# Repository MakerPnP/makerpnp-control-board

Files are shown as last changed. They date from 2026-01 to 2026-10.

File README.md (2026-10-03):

<div align="center">







MakerPnP

</div>

# MakerPnP - Control Board

The system is designed to be a fully-featured, and expandable system for pick-and-place machines. Additionally, it is a
drop-in replacement for CHMT32/48 VA/VB machines and existing cables can be used without rewiring and uses the same
mounting holes.

The system can be used for new PnP machines, or retro fitted to existing ones.

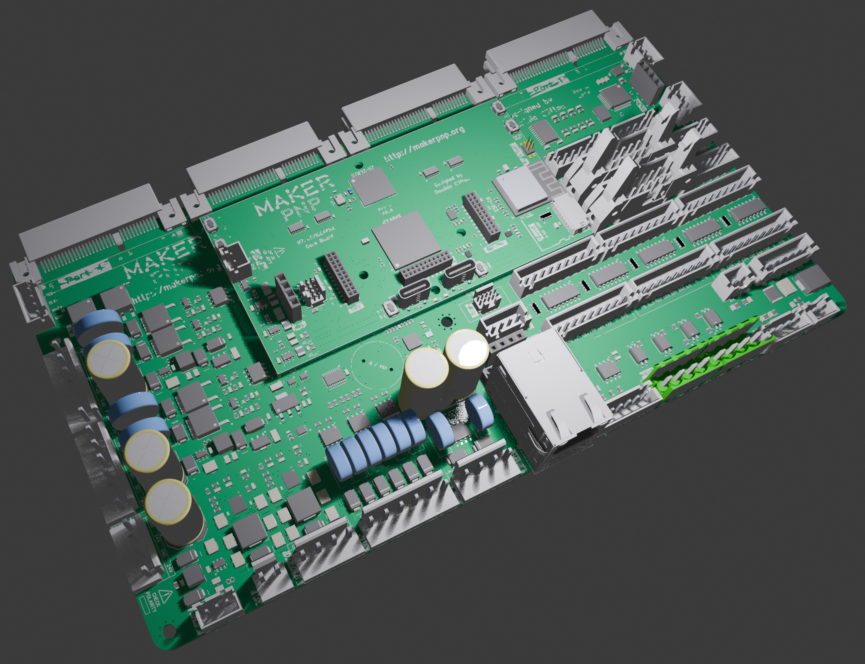
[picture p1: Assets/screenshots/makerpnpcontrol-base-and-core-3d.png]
MakerPnPControl Base and Core PCBs


The system is comprised of two main PCBs, called 'base' and 'core'. A 'core' has the processors and the 'base' has the
connectors for the machine, power-supply circuits, output drivers, protection circuits and other IO circuits and
connectors.  The base board also has expansion slots for things like stepper motor drivers.

The system will use the MakerPnP software and firmware, which is cross-platform and written in Rust. For further details
on the software refer to the following two source repositories:

* Planning software: https://github.com/MakerPnP/makerpnp
* Machine UI software and firmware: https://github.com/MakerPnP/machine

## User Features

* 6 A/B/Z (ABN) differential encoder inputs.
* 8 stepper motor transceiver-driven DIR/STEP signal pairs in 2 banks of 4.
* Emergency stop input on a dedicated hardware interrupt.
* 2x opto-coupled outputs.
* 2x opto-coupled inputs.
* Buzzer
* 8x 5V digital inputs. (end stops, etc)
* 2x 5V 6A regulators, 24V input.
* 5V output connector, e.g. for powering a Raspberry Pi 5.
* 7V output, e.g. for powering head-mounted devices.
* 8x 24V PWM controlled fused and flyback protected outputs.
* 2 pairs of two isolated 48V PWM capable fused and flyback protected outputs. (4x total). e.g. for pumps, heaters, etc.
* Load-cell amplifier.
* 10/100MBit Ethernet (in addition to the Wifi)
* RS422 for remote comms.
* Integrated 7 port USB hub.
* 2x FD-CAN 8Mbps ports.
* 2x I2C muxes and 2 port muxed I2C connector with 4 int signals. (great for identical sensors)
* 4x analog inputs (e.g. for Vacuum, Blow + 2 spare)
* Buttons on the CPU board, with break-out connectors on the main board.
* ETH link/activity LED break-out connector.
* USB connector.

## Expansion port system

The base board features 4x 64-pin expansion slots, each slot has enough signals for driving multiple stepper motors
per board, or for your other expansion ideas.

Each port has the following:
* 2 hardware UARTS.
* 1x SPI + 2x CS pins.
* 1x muxed I2C.
* 2x muxed analog inputs.
* 2x sets of ABN encoder signals. 
* 2x sets of DIAG0/DIAG1 signals.
* 2x 4 channel timers (e.g. for PWM, or 4x pairs of step/direction)
* Clock signals.
* Debug signals.
* Interrupt/Wake signals.
* Card insertion detection system.
* CAN H/L signals.
* USB port.
* 24V and 3.3V inputs.

Additionally, the base board as an RGB led physically located next to each port.

Expansion boards are planed for popular stepper motor drivers.

The slots are at the same physical height as the main board, due to the use of edge-mounted connectors.
Expansion slots can be combined. e.g. it is possible to design a board that plugs into 1,2,3 or 4 ports at the same time.
Note: For high-current expansion boards, it's advised to use power connectors on the expansion board itself.

## Expansion header system

The CPU board features 3 expansion sockets, to allow the connection of expansion cards or debug/development equipment
such as:

* 16 channel logic analyzer (via 16 dedicated FPGA pins).
* additional memory.
* additional sensors.
* other peripherals.

## Developer features

* The cpu/core board expansion headers also allow FPGA flash programming, ESP-C6 programming, H7 programming.
* Debug headers and ports (SWD).
* Boot buttons for H7 and C6.
* Cold-boot select buttons for the FPGA.

## Technical features

* 2 PCB system, a base board and a core board.
* STM32H725IG 550Mhz CPU, 1MB Flash, 564KB RAM (176+25 pin BGA)
* ICE40HX8K FPGA, 7680 logic cells, 128kbit RAM (256 pin BGA)
* ESP32-C6 module, 160Mhz, 4MB Flash, 512KB RAM, Wifi-6, RISC-V, BT 5 LE
* 16MBit shared flash.
* Base board uses 2oz copper 4L PCB.
* Core board used 1oz copper 6L PCB.
* Dedicated 4-bit hardware bus between H7 and FPGA. (OctoSPI1)
* Second 4-bit hardware bus between H7, FPGA, C6 and shared flash.  (OctoSPI2) 

The goal is to make accessing the FPGA and C6 from the H7 seamless by memory mapping them into the H7's address space
using OctoSPI, thus making it possible to send data to/from the FPGA and C6 without a complicated communication protocol.

## Firmware

Firmware is work-in-progress, join the MakerPnP discord server to find out the latest information!

## Status

This status is updated periodically, visit the discord server for the latest information.

### Status overview

| Functionality | Status |
|---|---|
| Base board main VRegs | ✅ - Working |
| Core board main VRegs | ✅ - Working |
| Base board to Core board connectors | 🚧 - Fit is perfect, not all IO lines tested yet |
| H7 Programming Port | ✅ - Working |
| H7 DFU button | ✅ - Working |
| C6 Enable button | ✅ - Working |
| C6 Boot button | ✅ - Working |
| C6 UART Pads | ✅ - Working |
| C6 Activity LED | ✅ - Working, blinky test code flashed via USB port and blinks LEDs |
| STM32H735 | 🚧 - Not all IO lines tested yet |
| ICE40HX8K | 🚧 - Not all IO lines tested yet |
| ESP32-C6 | 🚧 - Not all IO lines tested yet |
| USB hub | ✅ - Detected in Windows, H7 DFU + C6 JTAG working |
| Base board USB sockets | ✅ - Main up-stream socket working, spare hub USB port working | 
| Core board cable bus switches | ✅ - Working, cable works when connected, usb by hub works when cable disconnected |
| Flash | 🚧 - Works with H7 and FPGA, C6 connection untested |
| Ethernet | ✅ - Working well with Embassy-net/SMOL |
| Logic Analyzer Port | ✅ - All 16 IO signals working |
| Digital IO (DIN1-8) | ✅ - Working |
| Buttons | 🚧 - Working, but FPGA cold-boot selection not tested |
| LEDs (2x Activity) | ✅ - Working |
| Buzzer | ✅ - Working |
| Expansion Ports | 🚧 - Port 1 SPI + Wake + CLK + Step1/Dir1 (via mux) working |
| Expansion card detection circuit | ✅ - Working |
| Base board detection circuit | ✅ - Working |
| Timer Muxes | ✅ - Working, signals from FPGA or MCU can be selected |
| Master Reset button | ✅ - Working, powers off Core board regs when pressed |
| TMC5160 Stepper Motor | 🚧 - TMC5160 spins motors, external encoders inputs not tested yet. |
| Base board encoder sockets | ✅ - Working, tested with a 17HS24-2004-ME1K NEMA 17 stepper motor with encoder |
| Emergency stop input | ✅ - Working |
| Base board WS2812 LEDs | ✅ - Working |
| Base board WS2812 external LEDs | ✅ - Working |
| PWM outputs OT1-8 | ✅ - Working via flexible FPGA timer / pwm generation peripheral. | 
| PWM outputs PM1-4 | ✅ - Working via flexible FPGA timer / pwm generation peripheral. |
| HX717 load cell sensor | ✅ - Working. FPGA peripheral working. |
| BCDE/XYZF outputs | ✅ - Working, 8-motor stepper control with sequence based ramp/cruise and pause support |
| Analog In (AIN_VAC/AIN_EXT) | ✅ - Working |
| Analog In Mux (expansion ports 1-4) | ✅ - Working |
| DDIF socket | 🚧 - Not tested, but IC that signals are routed through is working, since encoders work |
| Optical I/O | ✅ - Working. Using 5V supply and 1k0 to GND via buttons for inputs. |
| EXP1 port | 🚧 - Not all IO lines tested yet |
| EXP2 port | 🟦 - Not tested |
| I2C muxes | ✅ - Working.  Both muxes responsive.  One mux tested with 2 pressure sensors that have the same address |
| Pressure sensors | ✅ - Working.  Used XGZP6895D 100KPG and 100KPGN variants (0-100kPa and -100-0kPa respectively) |
| External I2C socket | 🟦 - Not tested |
| External Link/Activity LED socket | 🟦 - Not tested |
| External buttons socket | 🟦 - Not tested |
| Wifi | 🟦 - Not tested |
| SDCard | 🟦 - Not tested |
| CAN 1 | 🟦 - Not tested |
| CAN 2 | 🟦 - Not tested |
| RS422 | 🟦 - Not tested |

### Status log

2026/06/23
 - Much IO is verified and working, code is being written for the FPGA and MCU to validate the hardware.
 - Memory mapped OctoSPI between H7 and FPGA is working well.
 - Stepper motor drivers are working well.

2026/05/30
 - Verification of the hardware is well underway.
 - Errata and Revision history files have been created.

2026/05/06
 - The base, core and stepper1 boards were delivered.

2026/03/13
 - An order for a very small batch of the base board has been placed.
 - the ICE40HX caBGA256 are in short supply, suppliers have 40 week lead times, an order has been placed for a small 
   quantity before suppliers run out.
 - An order for a small batch of the core boards will be placed ASAP.

## Manufacturing files

Refer to PCB Revision History / Errata files before using any files here.

The repo contains files that can be used for manufacturing, however do NOT use any files for manufacturing
PCBs.  Files in the repo are only good for manufacturing when they have been tagged with a git commit that says
'Release To Manufacturing' (RTM).  This is because commits to this repo may make changes to the schematic without
updating the PCB, changes the the PCB without re-exporting gerber or placement files and so on.  Also, there is a lag
between when files are used for manufacturing and when testing and validation is performed.

Example tags that were used for the first round of manufacturing:
```
RTM-MakerPnPBase-RevA-20260313-0241
RTM-MakerPnPCore-RevA-20260313-0242
RTM-MakerPnPCore-RevA-20260405-0022
RTM-MakerPnPStepper1-RevA-20260327-1304
RTM-MakerPnPStepper1-RevA-20260330-0052
```

## Building BOM variants

The MakerPnP `variantbuilder_cli` tool is used to take the exported DipTrace PnP files, along with the parts,
substitutions, and part mapping files, to produce PnP files that use actual parts that can be ordered and placed.

e.g. the schematic might say `CAP_0402`, and `100nF 6.3V 0402`, but additional information is added by substitution rules and
part mappings in order to end up with this:

```
├── C1 (name: 'CAP_0402', value: '100nF 6.3V 0402')
│   └── Substituted (name: 'CAP_0402', value: '100nF 6.3V 0402 X7R 10%'), by (name_pattern: 'CAP_0402', value_pattern: '100nF 6.3V 0402'), comment: 'Use X7R 10% by default'
│       └── Substituted (name: 'CAP_0402', value: '100nF 16V 0402 X7R 10%'), by (name_pattern: 'CAP_0402', value_pattern: '100nF 6.3V 0402 X7R 10%'), de-rate: 'from 6.3V to 16V'
│           └── manufacturer: 'Samsung Electro-Mechanics', mpn: 'CL05B104KO5NNNC' (Auto-selected)
```

Here's how the tools are can be run (from their corresponding directories):
```
$ variantbuilder_cli @MakerPnPControl-core-PnP_variant1.args
$ variantbuilder_cli @MakerPnPControl-PnP_variant1.args
```

Note: the arguments are contained within the `.args` files for easy editing and maintainability.

## Links

Please subscribe to be notified of live-stream events so you can follow the development process.

* Patreon: https://www.patreon.com/MakerPnP
* Source: https://github.com/MakerPnP
* Discord: https://discord.gg/ffwj5rKZuf
* YouTube: https://www.youtube.com/@MakerPnP
* X/Twitter: https://x.com/MakerPicknPlace

## Authors

* Dominic Clifton - Project founder and primary maintainer.

## License

CC-BY-NC - https://creativecommons.org/licenses/by-nc/4.0/

## Contributing

If you'd like to contribute, please raise an issue or a PR on the github issue tracker, work-in-progress PRs are fine
to let us know you're working on something, and/or visit the discord server.  See the Links section above.

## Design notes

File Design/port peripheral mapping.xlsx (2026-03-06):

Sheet: UFBGA176+25 Ports
Port | Timer 1 | EXTIs | Timer 2 | EXTIs | Timer1 to Timer 2 signal | Timer 2 to Timer 1 signal | SPI or DIAG0/1 | EXTIs | UART A | EXTIs | UART B | EXTIs | CH3/4 Extis
1 | TIM1 | 9,11,13,14 | TIM2 | 0,3,10,11 | ITR0 | ITR1 | SPI2 | 3,12,14,15 | USART1 | 9,10 | UART8 | 0,1 | 13,14,10,11
2 | TIM3 | 0,1,5,6 | TIM24 | 11,12,13,14 | ITR2 | ITR12 | SPI4 | 4,5,6,12 | USART3 | 8,9 | USART2 | 5,6 | 5,6,13,14
3 | TIM8 | 6,7,8,9 | TIM5 | 3,10,11,12 | ITR1 | ITR3 | SPI3 | 2,10,11,15 | UART5 | 2,12 | USART10 | 2,3 | 8,9,11,12
4 | TIM4 | 6,7,14,15 | TIM23 | 0,1,2,3 | ITR3 | ITR13 | SPI5 | 6,6,8,9 | UART9 | 0,1 | UART7 | 7,8 | 14,15,2,3
ALL UART B EXTIS are usable when using SPI, a single UART or timers for comms
All Timer 1's have interconnects to Timer 2's (Table 94, Peripheral interconnect matrix details)
All used EXTIs: |  | 0,1,2,3,4,5,6,7,8,9,13,14,15
Port 1 and 3 have higher priority UART EXTIs than Port 2 and 4
Scenarios
1 | Two large TYPE A cards plugged into ports 1/2 and 3/4.
2 | 2x TYPE B cards plugged into port 1 and 3 + 2x TYPE C cards plugged into port 2 and 4
3 | 4x TYPE C cards plugged into ports 1-4
4 | 4x TYPE D cards plugged into ports 1-4
5 | 2x TYPE E cards plugged into ports 2 and 4
 | Other variations/combinations possible with some signals going to the FPGA instead of the MCU.
TYPE A | 1 advanced timer, 1 normal timer, 2x32 bit timers with 4 encoders, 2 SPI + 2 HW NSS, 2 UARTS
TYPE B | advanced timer, 32 bit timer, 2 encoders, 1 spi, 1 HW NSS, 2 uarts
TYPE C | normal timer, 32 bit timer, 2 encoders, 1 spi, 1 HW NSS, 2 uarts
TYPE D | normal timer, 32 bit timer, 2 encoders, 1 spi, 1 HW NSS, 1 uart, 2 exti |  |  |  |  |  | 2xTMC5160 | Encoder signals go to TMC5160
TYPE E | 2 uarts, 2 ABN encoders,bit-bash/MDMA 2 pairs of step/dir on spi pins |  |  |  |  |  | 2xTMC2209 | ABN encoder signals on CH1/2/4 or FPGA encoders, use 2nd UART for 2xEXTI (2xDIAG0), FPGA for index.
Remarks
 | FPGA and MCU share a flash chip. MCU must not drive signals when FPGA boots, SS needs to be correct on boot to tell FPGA how to use the SPI, Flash WP and HOLD need to be correct too.
 | Flash is programmed by the MCU, via OCTOSPI.
 | Flash can be used by the MCU after the FPGA has booted, memory mapped if needed.
 | Backup FPGA images, configuration data and other stuff can be stored on the flash.
 | MCU can communicate with FPGA using SPI pins once FPGA is booted, as long as the FPGA implements an SPI peripheral on the same pins.
 | Need LED on the CDONE signal
 | Need a second SPI CS pin for the FPGA to be able to address either the flash or the FPGA.
 | Each card can have a small I2C flash chip for identification purposes.
 | CDONE used as an input while programming, and as an EXTI afterwards, and can have an LED.

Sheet: UFBFA176+25 Peripherals
Peripheral/IO | Features | Usage | Pins |  |  |  | Pin numbers | Sorted pin numbers
 |  |  | CH1 | CH2 | CH3 | CH4
TIM1 | Advanced,Encoder,16bit,DMA,4CH | Port 1 Encoder A/B/N + NSS2 | PE9 | PE11 | PE13 | PE14 | 9,11,13,14 | 9,11,13,14
TIM2 | Encoder,32bit,DMA,4CH | Step/Dir/Step/Dir | PA0 | PB3(JTDO/TRACESWO) | PB10 | PB11 | 0,3,10,11 | 0,3,10,11
TIM3 | Encoder,16bit,DMA,4CH | Port 2 Encoder A/B/N + NSS2 | PA6 | PB5 | PB0 | PB1 | 6,5,0,1 | 0,1,5,6
TIM4 | Encoder,16bit,DMA,4CH | Port 4 Encoder A/B/N + NSS2 | PB6 | PB7 | PD14 | PD15 | 6,7,14,15 | 6,7,14,15
TIM5 | Encoder,32bit,DMA,4CH | Step/Dir/Step/Dir | PH10 | PH11 | PH12 | PA3 | 10,11,12,3 | 3,10,11,12
TIM6 | DMA,DAC | DAC | PA4 |  |  |  | 4 | 4
TIM7 | DMA,DAC | DAC | #N/A
TIM8 | Advanced,Encoder,16bit,DMA,4CH | Port 3 Encoder A/B/N + NSS2 | PC6 | PC7 | PC8 | PC9 | 6,7,8,9 | 6,7,8,9
TIM12 | NoDMA,2CH | Embassy to use no support for TIM6/7/13/14/16/17 | NONE | NONE | NONE | NONE
TIM13 | NoDMA,1CH |  | NONE | NONE | NONE | NONE
TIM14 | NoDMA,1CH |  | NONE | NONE | NONE | NONE
TIM15 | DMA,2CH | Use to drive MDMA to generate 16 step/dir signals on SPI pins | NONE | NONE | NONE | NONE
TIM16 | DMA,1CH | Port 2 / EXPANSION PORT | PB8 | NONE | NONE | NONE | 8 | 8
TIM17 | DMA,1CH | Port 4 / EXPANSION PORT | PB9 | NONE | NONE | NONE | 9 | 9
TIM23 | Encoder,32bit,DMA,4CH | Step/Dir/Step/Dir | PF0 | PF1 | PF2 | PF3 | 0,1,2,3 | 0,1,2,3
TIM24 | Encoder,32bit,DMA,4CH | Step/Dir/Step/Dir | PF11 | PF12 | PF13 | PF14 | 11,12,13,14 | 11,12,13,14
TIM1_ETR |  | Port 1 / EXPANSION PORT | PG5
TIM8_ETR |  | Port 3 / EXPANSION PORT | PG8
 |  |  | OUT1 | OUT2 | EXTI9
DAC1 |  | EXPANSION PORT | PA4 | #N/A | PH9
 |  |  | SCK | MISO | MOSI | NSS
SPI1 |  | EXPANSION PORT | PA5 | PB4(NJTRST) | PD7 | #N/A
SPI2 |  | Port 1 | PD3 | PB14 | PB15 | PB12 | 3,14,15,12 | 3,12,14,15
SPI3 |  | Port 2 | PC10 | PC11 | PB2 | PA15(JTDI) | 10,11,2,15 | 2,10,11,15
SPI4 |  | Port 3 | PE12 | PE5 | PE6 | PE4 | 12,5,6,4 | 4,5,6,12
SPI5 |  | Port 4 | PH6 | PF8 | PF9 | PF6 | 6,8,9,6 | 6,6,8,9
SPI6 |  |  | #N/A | #N/A | #N/A | #N/A
Need 2x SW NSS for either SPI1 or SPI6
SPI1_NSS_SW_1 |  | EXPANSION PORT | PD10
SPI1_NSS_SW_2 |  | EXPANSION PORT | PF5
SPI2_NSS_2 |  |  | PG3
SPI3_NSS_2 |  |  | PG2
SPI4_NSS_2 |  |  | PG7
SPI5_NSS_2 |  |  | PG15
SPI6_NSS_SW_1 |  | WIFI | #N/A
SPI6_NSS_SW_2 |  | EXPANSION PORT | #N/A
Used GPIO ports for SPI |  |  | A,B,C,D,E,F,H
 |  |  | P1_DQS | P1_NCS | P1_CLK | P1_NCLK | P1_IO0 | P1_IO1 | P1_IO2 | P1_IO3
OCTOSPI1 | permanently memory mapped | FPGA | #N/A | PG6 | PF10 | #N/A | PD11 | PD12 | PC2 | PD13
 |  |  | P2_DQS | P2_NCS | P2_CLK | P1_NCLK | P1_IO4 | P1_IO5 | P1_IO6 | P1_IO7
OCTOSPI2 | conditionally memory mapped | FLASH - NCS to flash and ESP32-C6 FSPIQ and FPGA SPI_SS_B | #N/A | PG12 | PF4 | #N/A | PD4 | PH3 | PC3 | PE10
OCTOSPI2_NCS_2 | conditionally memory mapped | WIFI | PH15
OCTOSPI2_NCS_3 | conditionally memory mapped | EXPANSION_PORT | PE15
OCTOSPI2_NCS_4 | conditionally memory mapped | FPGA | PH1-OSC_OUT
^ NOTE: all OCTOSPI_NCS_x pins are on EXTI15 pin Px15 so use here is flexible
RCC_OSC_IN |  | TCXO, single pin | PH0-OSC_IN
 |  |  | RX | TX
USART1 |  | Stepper 1 | PA10 | PA9 |  |  | 10,9 | 9,10
USART2 |  | Stepper 2 | PD6 | PD5 |  |  | 6,5 | 5,6
USART3 |  | Stepper 3 | PD9 | PD8 |  |  | 9,8 | 8,9
UART4 |  | Head communication (RS422, no flow control) | PD0 | PD1 |  |  | 0,1 | 0,1
UART5 |  | Stepper 4 | PD2 | PC12 |  |  | 2,12 | 2,12
USART6 |  | EXPANSION PORT | PG9 | PG14 |  |  | 9,14 | 9,14
UART7 |  | Stepper 6 | PE7 | PE8 |  |  | 7,8 | 7,8
UART8 |  | Stepper 7 | PE0 | PE1 |  |  | 0,1 | 0,1
UART9 |  | Stepper 5 | PG0 | PG1 |  |  | 0,1 | 0,1
USART10 |  | Stepper 8 | PE2 | PE3 |  |  | 2,3 | 2,3
 |  |  | RX | TX
FDCAN1 |  | Port communications | PH14 | PH13
FDCAN2 |  |  | #N/A | #N/A
FDCAN3 |  | Head/Feeder communications | PG10 | PF7
 |  |  | SDA | SCL
I2C1 |  |  | #N/A | #N/A
I2C2 |  | Muxed between ports | PH5 | PH4
I2C3 |  | EXPANSION PORT | PH8 | PH7
I2C4 |  |  | #N/A | #N/A
EXTI0 |  | UART8_RX | PE0
EXTI1 |  | UART8_TX | PE1
EXTI2 |  | USART10_RX | PE2
EXTI3 |  | USART10_TX | PE3
EXTI4 |  | EXTI4_EMERGENCY_STOP | PG4
EXTI5 |  | USART2_TX | PD5
EXTI6 |  | USART2_RX | PD6
EXTI7 |  | UART7_RX | PE7
EXTI8 |  | UART7_TX | PE8
EXTI9 |  | EXTI9_DAC | PH9
EXTI10
EXTI11
EXTI12
EXTI13 |  | EXTI13_WIFI | PC13
EXTI14 |  | EXTI14_FPGA_INT | PC14-OSC32_IN
EXTI15 |  | EXTI15_FPGA_CDONE | PC15-OSC32_OUT
EXTI0,EXTI1,EXTI2,EXTI3,EXTI4,EXTI5,EXTI6,EXTI7,EXTI8,EXTI9,EXTI13,EXTI14,EXTI15 | 0,1,2,3,4,5,6,7,8,9,13,14,15
 |  | Devices on expansion port can trigger MCU action since the FPGA is an IO expander
DIGITAL_IN_1 |  |  | #N/A
DIGITAL_IN_2 |  |  | #N/A
DIGITAL_IN_3 |  |  | #N/A
DIGITAL_IN_4 |  |  | #N/A
ANALOG_IN_1 |  | Use for Analog MUX output 1 (mux inputs go to ports 1-4) (3v3 only) | PA0_C
ANALOG_IN_2 |  | Use for Analog MUX output 2 (mux inputs go to ports 1-4) (3v3 only) | PA1_C
ANALOG_IN_3 |  | EXPANSION PORT (3v3 only) | PC2_C
ANALOG_IN_4 |  | EXPANSION PORT (3v3 only) | PC3_C
ANALOG_IN_5 |  | Vacuum sense 1 (5V tolerant) | PC0
ANALOG_IN_6 |  | Vacuum sense 2 (5V tolerant) | PH2
PWM_OUT_1 |  | EXPANSION PORT | PB8
PWM_OUT_2 |  | EXPANSION PORT | PB9
PWM_OUT_3 |  |  | #N/A
PWM_OUT_4 |  |  | #N/A
PWM_OUT_5 |  |  | #N/A
PWM_OUT_6 |  |  | #N/A
PWM_OUT_7 |  |  | #N/A
PWM_OUT_8 |  |  | #N/A
EXTI14_FPGA_CDONE |  | For LED too | #N/A
FPGA_CRESET_B |  |  | PF15
 |  |  | DM | DP | ID
USB_OTG_HS |  | Device only, connected to an on-board USB hub | PA11 | PA12 | #N/A
FPGA_DIGITAL_IN_1 |  | Drag pin limit
FPGA_DIGITAL_IN_1 |  | Y endstop
FPGA_DIGITAL_IN_1 |  | X endstop
FPGA_DIGITAL_IN_1 |  | Z cam endstop/center
FPGA_PWM_OUT_1 |  | Drag pin
FPGA_PWM_OUT_2 |  | Head down light
FPGA_PWM_OUT_3 |  | Vacuum switch 1
FPGA_PWM_OUT_4 |  | Vacuum switch 1
FPGA_PWM_OUT_5 |  | Work light
FPGA_PWM_OUT_6 |  | Up light
FPGA_PWM_OUT_7 |  | Vacuum pump
FPGA_PWM_OUT_8 |  | Blow pump
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

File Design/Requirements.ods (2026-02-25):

Requirements |  | Notes | Pin-out TODO | Old Done List
 | Fast MCU | STM32H725, TFBGA100, UFBGA 176+25, LQFP144 ?
 |  | H725 has 4x 32 bit timers (TIM2,TIM5,TIM23,TIM24), H743 only has 2 (TIM2, TIM5)
 | FPGA | iCE40HX8K-CT256, 0.8mm pitch 256-ball caBGA
 | Ethernet port | Connected to MCU
 | Ethernet LED port | 2x LED open-drain outputs + 3V3 + GND |  | Use FPGA to drive signals | Need some LED drivers conneted to the FPGA.
 | USB Hub | 8 ports. Main MCU, FPGA, Head MCU, 4x expansion slots, 1 for PC. FE2.1 chipset. Multi-TT. |  | MCU Done
 | Wifi Module/Flashing port | Header to allow for programming of FPGA and MCU and to support a WIFI module.
 |  | To allow for OTA firmware upgrades on main MCU/FPGA
 |  | Signals: MCU NRST, SPI, UART, FPGA programming + SPI + UART + reset, FPGA+WIFI int and CS.
 | IO swappable between MCU and FPGA | Via 3 pin jumpers per signal.
 |  | e.g. to allow either FPGA to drive stepper signals.
 | CHMT48VB compatible connectors | Only for NEEDED IO, not for ALL IO.
 |  | Must allow existing cables to be plugged in without any rewiring.
 | 4x Expansion connectors | Wire up some FPGA pins to each connector + select MCU peripherals
 |  | USB to each port, connect to primary USB interface on peripheral boards.
 |  | At least 2 sockets need sufficient signals to drive 2x 2.54" stepper motor sockets each, in HARDWARE. | DONE | DONE | DIAG0/1 on unused interface pins, with EXTI
 |  | If sufficient MCU peripherals remain, wire up remaining 2 sockets to support them too.
 |  | Ideally 1x 32 bit timer per socket. Ensure timers have encoder support. | DONE | DONE
 |  | 1x UART per socket. | DONE | DONE
 |  | 1x set of SPI SCK/MOSI/MISO pins per socket. With 2x CS pins. Ideally 1 SPI interface per socket with on hardware NSS signal. | TODO (need 1 extra pin per port) | DONE
 |  | 1x pair of SDA/SCL pins. Each socket shares the same I2C bus, e.g. for enumeration/detection. | DONE, using 4:1 bus switch though | DONE
 | Compatible head-connector | 2x PWM controlled outputs for lights | DONE, using DMA driven PWM | SEE BELOW
 |  | 1x PWM controlled output for drag pin solenoid | DONE, using DMA driven PWM | SEE BELOW
 |  | Input for Z center sensor | DONE | DONE
 |  | Input for Drag pin limit sensor | DONE | DONE
 |  | Input for X endstop | DONE | DONE
 |  | 2x Vacuum sensors (Analog, non-isolated) | DONE | DONE
 | Future head-connector | The idea is for an MCU on the head, with vacuum sensor, vacuum switches, lighting, etc.
 |  | [RS422|CAN|USB],5V, 24V, GND - head cable is LONG in this machine, ~2m | DONE, UART OR CAN from MCU, same pins on MCU | UART+CAN from MCU
 |  | 2+2 differential line driver inputs/outputs
 | Chassis digital inputs | Input for Y endstop | DONE | DONE
 | 2x 24V high current PWM controlled outputs | Vacuum pump and Blow pump | DONE, using dedicated PWM timers | DONE
 | 6x 24V medium current PWM controlled outputs | Drag pin solenoid, 3x lights, 2x vacuum switches. | DONE, using DMA driven PWM | DONE
 | 4x PWM fan headers | With RPM feedback | NOT ENOUGH FPGA pins, no space for connectors. | FPGA for PWM and RPM feedback
 |  | Ensure there are 4 PWM circuits connected to the FPGA.
 | 2x Differential Encoder inputs | CHMT48VB only has encoders on X + Y motors. | DONE, via FPGA | Use TIM23 + TIM24 (CH1/CH2 on each)
 |  | Use hardware timers for encoder sampling by hardware. |  | DONE
 | Emergency Stop Input | Should be connected to an EXTI pin and/or TIM_BK input | DONE, EXTI0 | DONE
 | Stepper motor outputs | X Step/Dir | DONE, Via PORT_1 Timer 1 CH1/2
 |  | Y Step/Dir | DONE, Via PORT_1 Timer 1 CH3/4
 |  | L Nozzle Step/Dir | DONE, Via PORT_3 Timer 1 CH1/2
 |  | R Nozzle Step/Dir | DONE, Via PORT_3 Timer 1 CH3/4
 |  | L Feeder Step/Dir | DONE, Via PORT_2 Timer 1 CH1/2
 |  | R Feeder Step/Dir | DONE, Via PORT_2 Timer 1 CH3/4
 |  | Spare Step/Dir 1 | DONE, Via PORT_3 Timer 1 CH1/2
 |  | Spare Step/Dir 2 | DONE, Via PORT_3 Timer 1 CH3/4
 | Buzzer | No need for PWM for it, but can if needed. | DONE
 | 5V 3A output, for Raspberry Pi 5
 |  | Comms for Raspberry Pi to use ethernet
 | 2x connectors for X/Y end-stops | To allow for optical limit switches to be used
 |  | Also to allow for better routing of the Y end-stop wire.
 |  | Rerouting requires purchase of male to female 2 pin XH cable and repinning it and wiring the socket from the cable to the existing harness.
 |  | 3v3, IN, GND
 | 4x Digital inputs 5V tolerant. | Non-isolated in CHMT design. | DONE,PC0,PC3,PH2,PH3 all FT_ha | DONE
 | Analog inputs AI1-4 may need to be 5V tolerant | Non-isolated in CHMT design. | PA0_C,PA1_C,PC2_C,PC3_C are all TT_a, 3v3 ONLY | DONE
 | 2x Digital expansion/pass-though connector. | The idea is that a simple pass-though PCB can be made to route signals between the MCU and FPGA and OR to an expansion connector.
 |  | i.e. MCU -> FPGA or Expansion, FPGA -> MCU or expansion.
 |  | Route all remaining FPGA pins to some high-density connector
 |  | Route remaining FPGA pins to some high-density connector
 |  | Ideally connectors arranged so that the board cannot be inserted incorrectly, even when the same plugs/sockets are used.
 |  | 5V, 3V3, GND, no 24V.
 | Logic expansion header (2.54mm) | Route some pins from the expansion/passthough connector to a logic expansion header
 |  | 24V, 5V, 3V3,GND
Would be nice
 | DCMI camera interface
 | I2C switch | For I2C vacuum sensors that have the same address | DONE, use a 4:1 bus switch on I2C3
 |  | Or enough I2C headers on STM32 I2C peripherals
 | 4x I2C headers | 3v3,GND,SDA,SCL
 | 2x 2.54" stepper motor sockets | But maybe just make a peripheral board, with 2 on each for now
 | 2x Opto Isolated outputs |  | DONE, noted on FPGA pins list
 | 2x Opto Isolated inputs |  | DONE, noted on FPGA pins list
 | 2-4x additional 24V high current PWM controlled outputs
 | 2-4x additional 24V medium current PWM controlled outputs
 |  | The idea is to use 16 GPIO pins (pin1-8 plus pin 9-16 from two ports, or pins 1-16 from a single port) so that PWM can be controlled for each pin via a DMA stream using the GPIO-ODR[H/L] registers.
 |  | Ideally divide 2 16 bit timers over those pins, so that some pins can be GPIO+DMA driven and others can be hardware driven.
Machine external facing ports
 | Front panel USB socket | For USB sticks, OTG.
 | Side/Rear Ethernet port
 | Side/Rear USB port
Make a small PCB to mount to the case
 | RJ45+USB in
 | RJ45+USB out
 | 2x LED input signals + 3v3 + GND
 | 2x LEDs on RJ45 connector
TODO
 | Think about additional FPGA connectors.
 | Think of uses for the 3 unused timers TIM13/14/16, each with capture compare. | Probably use 2 timers for 2 additional high current PWM outputs

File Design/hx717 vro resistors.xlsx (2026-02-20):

VRO | R1 | R2
4.44 | 30000 | 10000
4.7952 | 33200 | 10000
3.8739 | 24900 | 10000

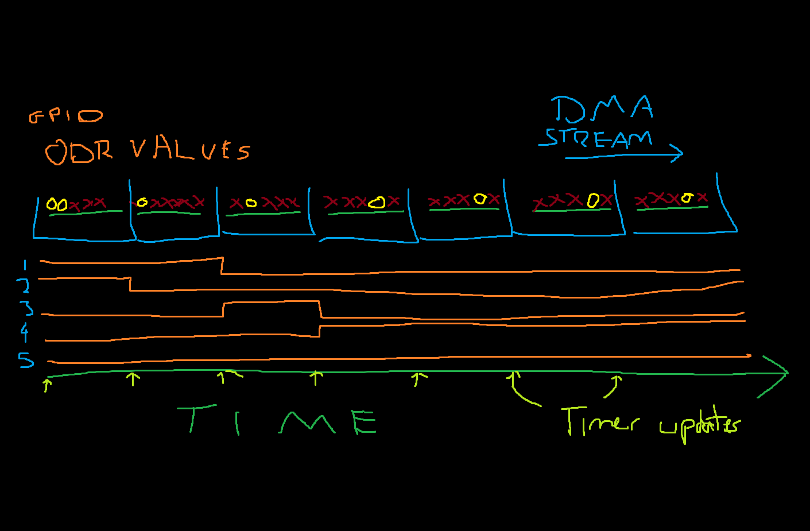
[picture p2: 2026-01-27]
Design/gpio dma for pwm signals.png

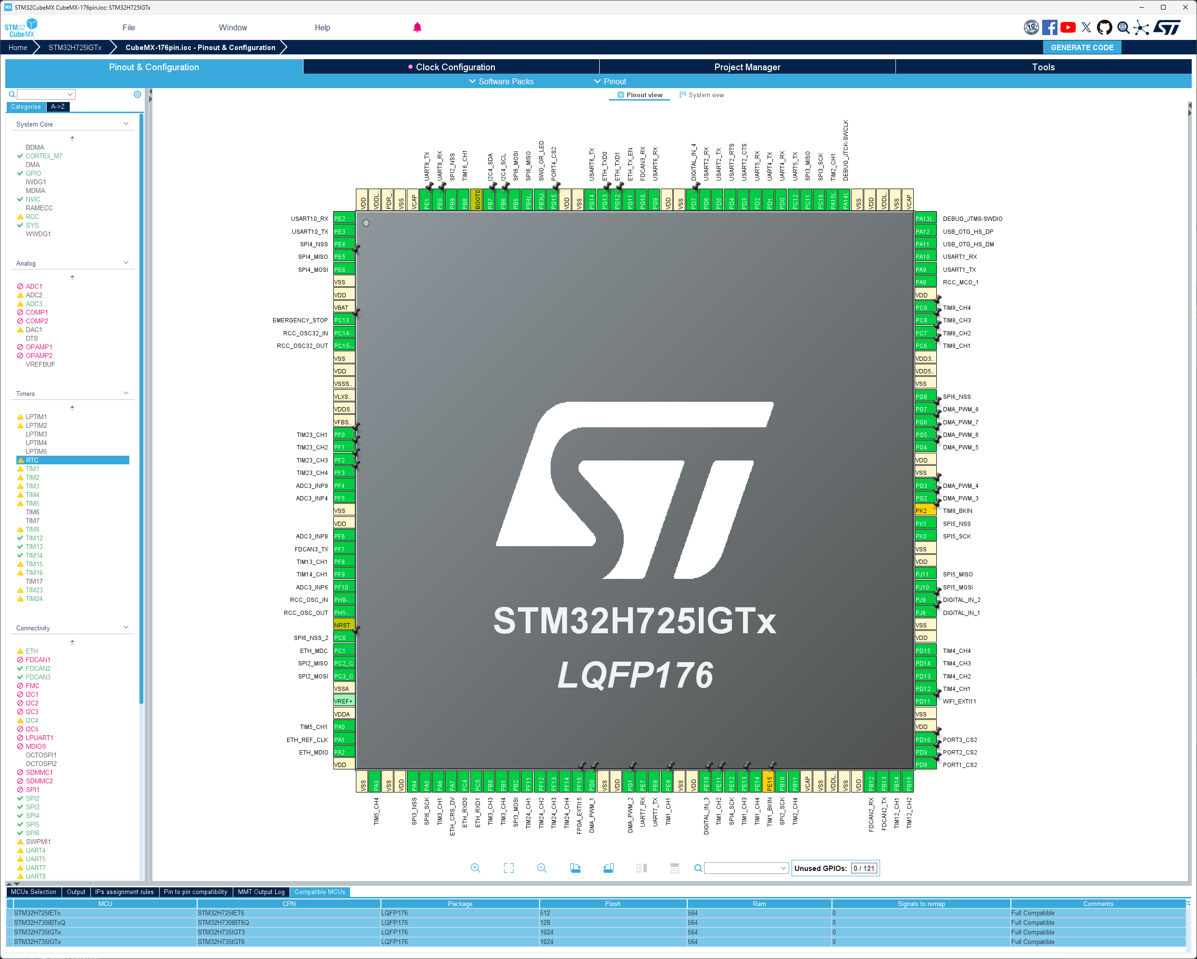
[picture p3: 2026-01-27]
Design/h725 pinout - 20260127.png

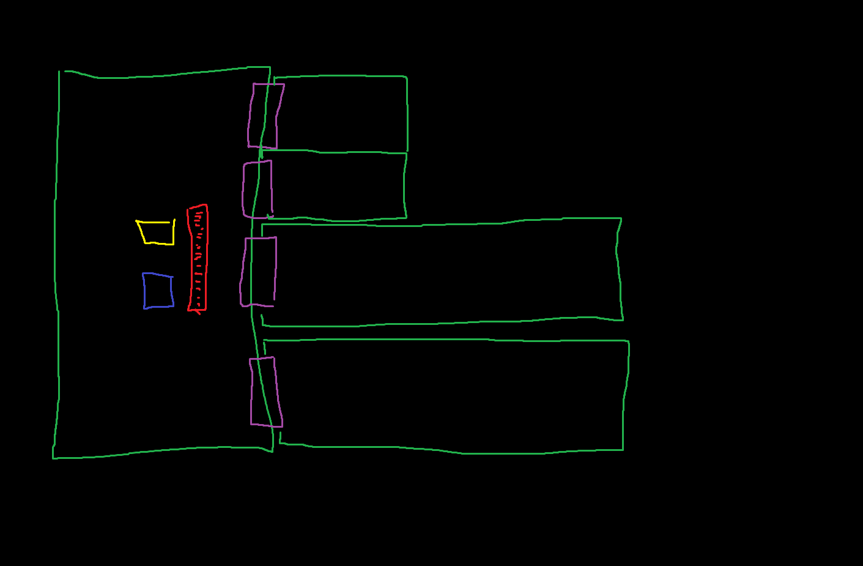
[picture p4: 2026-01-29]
Design/board-concept with jumpers and 4 ports.png

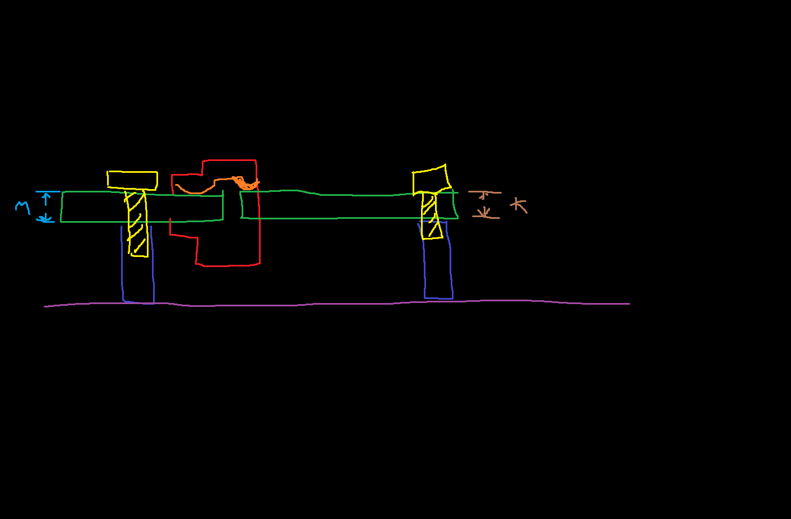
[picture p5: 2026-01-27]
Design/straddle connectors.png

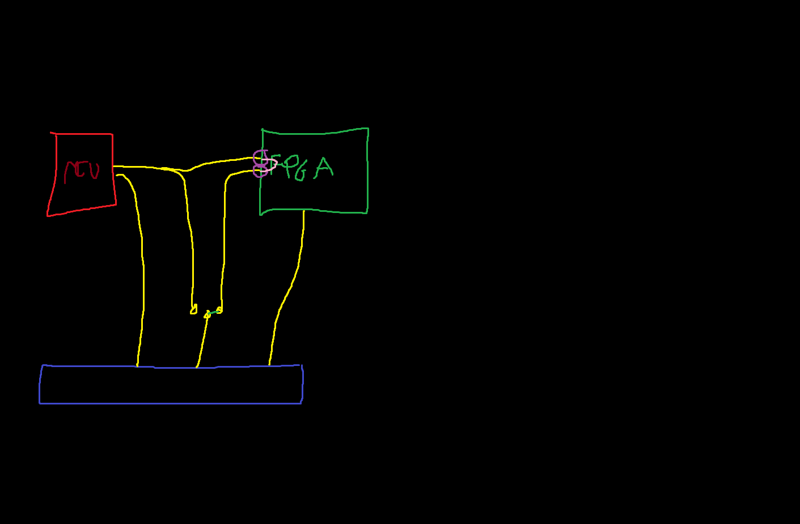
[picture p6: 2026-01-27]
Design/signal routing and selection.png

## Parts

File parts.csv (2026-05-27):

LCSC | Manufacturer | Mpn | Description
C193902 | Foshan NationStar Optoelectronics | NCD0603R5 | Red 65mW 0603 Light Emitting Diodes (LED) ROHS
C84266 | Foshan NationStar Optoelectronics | NCD0603B1 | blue 0603 Light Emitting Diodes (LED) ROHS
C84265 | Foshan NationStar Optoelectronics | NCD0603W1 | White light 0603 Light Emitting Diodes (LED) ROHS
C84267 | Foshan NationStar Optoelectronics | NCD0603G1 | Emerald 0603 Light Emitting Diodes (LED) ROHS
C84269 | Foshan NationStar Optoelectronics | NCD0603O1 | Orange 0603 Light Emitting Diodes (LED) ROHS
C84268 | Foshan NationStar Optoelectronics | NCD0603Y1 | yellow 0603 Light Emitting Diodes (LED) ROHS
C52923 | Samsung Electro-Mechanics | CL05A105KA5NQNC | 1uF ±10% 25V X5R 0402 Multilayer Ceramic Capacitors MLCC - SMD/SMT RoHS
C52923 | Samsung Electro-Mechanics | CL05A105KA5NQNC | 1uF ±10% 25V X5R 0402 Multilayer Ceramic Capacitors MLCC - SMD/SMT RoHS
C45783 | Samsung Electro-Mechanics | CL21A226MAQNNNE | 22uF 25V X5R ±20% 0805 Multilayer Ceramic Capacitors MLCC - SMD/SMT ROHS
C1525 | Samsung Electro-Mechanics | CL05B104KO5NNNC | 100nF 16V X7R ±10% 0402 Multilayer Ceramic Capacitors MLCC - SMD/SMT ROHS
C77004 | Murata Electronics | GRM155R61A475KEAAD | 10V 4.7uF X5R ±10% 0402 Multilayer Ceramic Capacitors MLCC - SMD/SMT ROHS
C96446 | Samsung Electro-Mechanics | CL10A106MA8NRNC | 10uF 25V X5R ±20% 0603 Multilayer Ceramic Capacitors MLCC - SMD/SMT ROHS
C97872 | Murata Electronics | GRM155R71H221KA01D | 220pF 50V X7R ±10% 0402 Multilayer Ceramic Capacitors MLCC - SMD/SMT ROHS
C107369 | Samsung Electro-Mechanics | CL05A225KP5NSNC | 10V 2.2uF X5R ±10% 0402 Multilayer Ceramic Capacitors MLCC - SMD/SMT ROHS
C19666 | Samsung Electro-Mechanics | CL10A475KO8NNNC | 16V 4.7uF X5R ±10% 0603 Multilayer Ceramic Capacitors MLCC - SMD/SMT ROHS
C19674255 | HCI | 8132H-50.000ML33DTL | -40℃~+85℃ 3.3V 50MHz CMOS ±2ppm SMD3225-4P Temperature Compensated Crystal Oscillators (TCXO) ROHS
C2843335 | WINBOND | W25Q16JVUXIQ | -40℃~+85℃ 100,000 cycles 10uA 133MHz 16Mbit 2.7V~3.6V 20 Years 3ms SPI USON-8-EP(2x3) NOR FLASH ROHS
C730151 | ST | STM32H725IGK6 | 32-bit Arm Cortex-M7 550 MHz MCU, up to 1 MB Flash memory, 564 KB RAM, 35 comms peripherals and analog interfaces
C113947 | MDD(Microdiode Semiconductor) | BAV21W | 1.25V@200mA 100nA@250V 200mA 250V 3A 500mW 50ns Independent SOD-123 Switching Diodes ROHS
C6037812 | Amphenol | 10164228-1001A1RLF | Header, 100 Position Board to Board Connector Surface Mount,P=0.4mm Gold
C21261228 | XKB Connection | X0408WVS-100A-LPV01 | -35℃~+85℃ 0.4mm 100P 2 300mA 30V Gold Phosphor Bronze Surface Mount,Vertical SMD,P=0.4mm Board-to-Board and Backplane Connector ROHS
C531031 | HRS | DF40C-100DP-0.4V(51) | Header, 100 Position Board to Board Connector Surface Mount,P=0.4mm Gold
C42376235 | G-Switch | GT-B0403MSV11-100B1101 | Header, 100 Position Board to Board Connector Surface Mount,P=0.4mm Gold
C7435219 | Amphenol | 10164227-1004A1RLF | Receptacle, 2 0.4mm Surface Mount,Vertical 100P SMD,P=0.4mm Arrays, Edge Type, Mezzanine (Board to Board) RoHS, 3.9mm
C19089295 | HCTL | HC-PBB40C-100DS-0.4V-3.0-02 | -40℃~+85℃ 0.4mm 100P 2 300mA 3mm Gold Slot Type Butting Surface Mount,Vertical SMD,P=0.4mm Board-to-Board and Backplane Connector ROHS
C7602567 | XKB Connection | X0408FVS-100F-LPV01 | -35℃~+85℃ 0.4mm 100P 2 300mA 30V Gold Phosphor bronze Surface Mount,Vertical SMD,P=0.4mm Board-to-Board and Backplane Connector ROHS, 3.9mm
C424649 | HRS | DF40HC(3.0)-100DS-0.4V(51) | Receptacle, 0.4mm Pitch, 1.5 to 4.0mm Height, Board-to-Board and Board-to-FPC Connectors, 2.9mm
C42376280 | G-Switch | GT-B0403FSV39-100B1101 | Receptacle, 100 Position Board to Board Connector Surface Mount,P=0.4mm Gold, 3.9mm
C3151749 | SHOU HAN | TYPE-C 16PLT-H10.0 | USB-C (USB TYPE-C) Receptacle Connector 16 Position Surface Mount
C50380694 | LCKELEC | LCK-TF-027H37508-WLG | -25℃~+85℃ Push-Pull 3.75mm Connector and Ejector MicroSD Card (TF Card) SMD PC Card Sockets RoHS
C7494852 | Yxcon | F343-1211A0CMUB1 | Female Header 22 Position 1.27mm Pitch Dual Row Surface Mount
C3975137 | HCTL | PM127-2-11-S-4.3 | -40℃~+105℃ 1.27mm 1.27mm 1A 2 22P 2x11P 4.3mm Phosphor bronze Square Hole Surface Mount,Vertical Top SMD,P=1.27mm Female Headers ROHS
C3975185 | HCTL | PZ127-2-02-S | Pin Header 4 Position 1.27mm Pitch Dual Row Surface Mount -40℃~+105℃
C2932107 | Samtec | FTSH-105-01-L-DV-K-P-TR | Pin Header 2 3.05mm -55℃~+125℃ 10P 1.27mm 1.27mm 2x5P SMD,P=1.27mm Headers, Male Pins RoHS
C3910547 | Taiyo Yuden | MCHK1608T2R2MKN | 1.2A 2.2uH 1.5A 292mΩ Multilayer inductor ±20% 0603 Fixed Inductors RoHS
C435392 | muRata | DFE252012F-1R0M=P2 | 3.3A 1uH 4.7A 40mΩ ±20% 1008 Fixed Inductors RoHS
C25744 | UNI-ROYAL(Uniroyal Elec) | 0402WGF1002TCE | -55℃~+155℃ 10kΩ 50V 62.5mW Thick Film Resistor ±1% ±100ppm/℃ 0402 Chip Resistor - Surface Mount ROHS
C25105 | UNI-ROYAL(Uniroyal Elec) | 0402WGF330JTCE | -55℃~+155℃ 33Ω 50V 62.5mW Thick Film Resistor ±1% ±100ppm/℃ 0402 Chip Resistor - Surface Mount ROHS
C25900 | UNI-ROYAL(Uniroyal Elec) | 0402WGF4701TCE | -55℃~+155℃ 4.7kΩ 50V 62.5mW Thick Film Resistor ±1% ±100ppm/℃ 0402 Chip Resistor - Surface Mount ROHS
C25905 | UNI-ROYAL(Uniroyal Elec) | 0402WGF5101TCE | -55℃~+155℃ 5.1kΩ 50V 62.5mW Thick Film Resistor ±1% ±100ppm/℃ 0402 Chip Resistor - Surface Mount ROHS
C25118 | UNI-ROYAL(Uniroyal Elec) | 0402WGF470JTCE | -55℃~+155℃ 47Ω 50V 62.5mW Thick Film Resistor ±1% ±100ppm/℃ 0402 Chip Resistor - Surface Mount ROHS
C17168 | UNI-ROYAL(Uniroyal Elec) | 0402WGF0000TCE | -55℃~+155℃ 0Ω 50V 62.5mW Thick Film Resistor ±1% ±800ppm/℃ 0402 Chip Resistor - Surface Mount ROHS
C25104 | UNI-ROYAL(Uniroyal Elec) | 0402WGF3300TCE | -55℃~+155℃ 330Ω 50V 62.5mW Thick Film Resistor ±1% ±100ppm/℃ 0402 Chip Resistor - Surface Mount ROHS
C25741 | UNI-ROYAL(Uniroyal Elec) | 0402WGF1003TCE | -55℃~+155℃ 100kΩ 50V 62.5mW Thick Film Resistor ±1% ±100ppm/℃ 0402 Chip Resistor - Surface Mount ROHS
C27009 | UNI-ROYAL(Uniroyal Elec) | 0402WGF4533TCE | -55℃~+155℃ 453kΩ 50V 62.5mW Thick Film Resistor ±1% ±100ppm/℃ 0402 Chip Resistor - Surface Mount ROHS
C25076 | UNI-ROYAL(Uniroyal Elec) | 0402WGF1000TCE | -55℃~+155℃ 100Ω 50V 62.5mW Thick Film Resistor ±1% ±100ppm/℃ 0402 Chip Resistor - Surface Mount ROHS
C728884 | YAGEO | YC164-FR-072KL | 2kΩ 4 62.5mW 8 ±1% ±200ppm/℃ 0603x4 Resistor Networks, Arrays ROHS
C22775 | UNI-ROYAL(Uniroyal Elec) | 0603WAF1000T5E | -55℃~+155℃ 100mW 100Ω 75V Thick Film Resistor ±1% ±100ppm/℃ 0603 Chip Resistor - Surface Mount ROHS
C22936 | UNI-ROYAL(Uniroyal Elec) | 0603WAF100KT5E | -55℃~+155℃ 100mW 1Ω 75V Thick Film Resistor ±1% ±400ppm/℃ 0603 Chip Resistor - Surface Mount ROHS
C25091 | UNI-ROYAL(Uniroyal Elec) | 0402WGF2200TCE | -55℃~+155℃ 220Ω 50V 62.5mW Thick Film Resistor ±1% ±100ppm/℃ 0402 Chip Resistor - Surface Mount ROHS
C473612 | UNI-ROYAL(Uniroyal Elec) | HP06W2J0000T5E | -55℃~+155℃ 0Ω 200V 500mW Thick Film Resistor ±5% 1206 Chip Resistor - Surface Mount ROHS
C5117876 | G-Switch | GT-TC031A-H020-L1N | -30℃~+85℃ 1.6N 100,000 cycles 12V 2.9mm 2mm 3.9mm 50mA Black No Round Button SMD(SMT) Tab SPST Surface Mount,Vertical Without Bracket SMD,3.9x2.9mm Tactile Switches ROHS
C2934569 | Espressif Systems | ESP32-C3-MINI-1-H4 | -40℃~+105℃ -96dBm 2.4GHz 20.5dBm 3.3V On-board PCB Antenna SPI SMD,16.6x13.2mm WiFi Modules ROHS
C7362468 | Texas Instruments | TMUXHS221NKGR | -40℃~+125℃ 1.7pF 16us 2 2:1 3.3GHz 3V~3.6V 500ns 80ps 8Ω UQFN-10(1.4x1.8) Analog Switches, Multiplexers ROHS
C2875445 | Texas Instruments | SN3257QDYYRQ1 | -40℃~+125℃ 1.5V~5.5V 4 5Ω 95ns SPDT SOT-23-THN-16 Analog Switches, Multiplexers ROHS
C22445521 | Texas Instruments | TPS62A02PDDCR | -40℃~+125℃ 1 2.4MHz 2.5V~5.5V Buck Buck SOT-23-THIN-6 DC-DC Converters ROHS
C702185 | Texas Instruments | TPS3820-50DBVR | -40℃~+85℃ 1 15uA 2.5V、3V、3.3V、5V 200ms 4.55V Active Low Push-pull Voltage Monitor Yes Yes SOT-23-5 Supervisor and Reset ICs ROHS
C1521993 | Lattice | ICE40HX8K-CT256 | -40℃~+100℃ 131072bit 7680 960 CABGA-256 Programmable Logic Device (CPLDs/FPGAs) ROHS
C23067542 | G-Switch | GT-A2501WVD-102SBT01 | -25℃~+85℃ 1 1x2P 2 2.5mm 250V 2P 3A 7.1mm Beige Brass PA66 Through Hole Tin UL94V-0 XH Plugin,P=2.5mm Wire To Board Connector ROHS
C304036 | Walsin Tech Corp | 1812B472K202CT | 2kV 4.7nF X7R ±10% 1812 Multilayer Ceramic Capacitors MLCC - SMD/SMT ROHS
C1591 | Samsung Electro-Mechanics | CL10B104KB8NNNC | 100nF 50V X7R ±10% 0603 Multilayer Ceramic Capacitors MLCC - SMD/SMT ROHS
C487393 | Ymin | VKME1651J331MV | -55℃~+105℃ 1.58A@100kHz 10000hrs@105℃ 10mm 16.5mm 330uF 63V ±20% SMD,D10xL16.5mm Aluminum Electrolytic Capacitors - SMD ROHS
C15725 | Samsung Electro-Mechanics | CL10B104KC8NNNC | 100V 100nF X7R ±10% 0603 Multilayer Ceramic Capacitors MLCC - SMD/SMT ROHS
C170099 | Samsung Electro-Mechanics | CL32B475KBUYNNE | 4.7uF 50V X7R ±10% 1210 Multilayer Ceramic Capacitors MLCC - SMD/SMT ROHS
C1588 | Samsung Electro-Mechanics | CL10B102KB8NNNC | 1nF 50V X7R ±10% 0603 Multilayer Ceramic Capacitors MLCC - SMD/SMT ROHS
C1589 | Samsung Electro-Mechanics | CL10B103KB8NNNC | 10nF 50V X7R ±10% 0603 Multilayer Ceramic Capacitors MLCC - SMD/SMT ROHS
C96446 | Samsung Electro-Mechanics | CL10A106MA8NRNC | 10uF 25V X5R ±20% 0603 Multilayer Ceramic Capacitors MLCC - SMD/SMT ROHS
C14860 | Samsung Electro-Mechanics | CL31B106KAHNNNE | 10uF 25V X7R ±10% 1206 Multilayer Ceramic Capacitors MLCC - SMD/SMT ROHS
C77023 | Murata Electronics | GRM155R71H223KA12D | 22nF 50V X7R ±10% 0402 Multilayer Ceramic Capacitors MLCC - SMD/SMT ROHS
C29936 | Samsung Electro-Mechanics | CL10B105KA8NNNC | 1uF 25V X7R ±10% 0603 Multilayer Ceramic Capacitors MLCC - SMD/SMT ROHS
C5440143 | Samwha Capacitor | CS3225X7R476K160NRL | 16V 47uF X7R ±10% 1210 Multilayer Ceramic Capacitors MLCC - SMD/SMT ROHS
C6328904 | KYOCERA AVX | TAJA226M016RNJ | -55℃~+125℃ 16V 2.3Ω@100kHz 22uF ±20% 1206 Tantalum Capacitors ROHS
C155422 | Samsung Electro-Mechanics | CL05B104KA5NNNC | 100nF 25V X7R ±10% 0402 Multilayer Ceramic Capacitors MLCC - SMD/SMT ROHS
C5139656 | Samsung Electro-Mechanics | CL05B472KC5VPNC | 100V 4.7nF X7R ±10% 0402 Multilayer Ceramic Capacitors MLCC - SMD/SMT ROHS
C1653 | Samsung Electro-Mechanics | CL10C220JB8NNNC | 22pF 50V C0G ±5% 0603 Multilayer Ceramic Capacitors MLCC - SMD/SMT ROHS
C2166065 | Nichicon | UHW1H331MPD1TD | -40℃~+105℃ 10mm 20mm 330uF 50V ±20% Plugin, D10xL20mm Aluminum Electrolytic Capacitors - Leaded ROHS
C307449 | Samsung Electro-Mechanics | CL05C471JB5NNNC | 470pF 50V C0G ±5% 0402 Multilayer Ceramic Capacitors MLCC - SMD/SMT ROHS
C2480 | MDD(Microdiode Semiconductor) | SS14 | -55℃~+150℃ 1A 25A 300uA@40V 40V 550mV@1A Independent SMA(DO-214AC) Schottky Diodes ROHS
C15874 | MDD(Microdiode Semiconductor) | SS310 | -55℃~+125℃ 100V 3A 500uA@100V 850mV@3A Independent SMA(DO-214AC) Schottky Diodes ROHS
C138782 | MDD(Microdiode Semiconductor) | SMAJ7.0A | -65℃~+150℃ 12V 200uA 33.3A@10/1000us 400W@10/1000us 7V 8.6V TVS Unidirectional DO-214AC(SMA) ESD and Surge Protection (TVS/ESD) ROHS
C113952 | MDD(Microdiode Semiconductor) | SMAJ5.0A | -65℃~+150℃ 400W@10/1000us 43.5A 5V 7V 800uA 9.2V TVS Unidirectional DO-214AC(SMA) ESD and Surge Protection (TVS/ESD) ROHS
C113957 | MDD(Microdiode Semiconductor) | SMAJ12A | -65℃~+150℃ 12V 14.7V 19.9V 1uA 20.1A@10/1000us 400W@10/1000us TVS Unidirectional DO-214AC(SMA) ESD and Surge Protection (TVS/ESD) ROHS
C113962 | MDD(Microdiode Semiconductor) | SMAJ24A | -65℃~+150℃ 10.3A@10/1000us 1uA 24V 29.5V 38.9V 400W@10/1000us TVS Unidirectional DO-214AC(SMA) ESD and Surge Protection (TVS/ESD) ROHS
C173502 | MDD(Microdiode Semiconductor) | SMAJ48A | -65℃~+150℃ 1uA 400W@10/1000us 48V 5.2A@10/1000us 58.9V 77.4V TVS Unidirectional DO-214AC(SMA) ESD and Surge Protection (TVS/ESD) ROHS
C1973855 | STMicroelectronics | SMAJ48A-TR | -55℃~+150℃ 100V 1uA 23A@8/20us 400W 48V 56.1V IEC 61000-4-2、IEC 61000-4-5 TVS Unidirectional SMA(DO-214AC) ESD and Surge Protection (TVS/ESD) ROHS
C1976142 | Vishay Intertech | SMCJ6.0A-E3/57T | -55℃~+150℃ 1.5kW@10/1000us 10.3V 145.6A 1mA 6.67V 6V TVS Unidirectional SMC(DO-214AB) ESD and Surge Protection (TVS/ESD) ROHS
C343998 | BORN | PESD5V0S2BT | 120pF 16V 2 20A 300W@8/20us 500nA 5V 6V ESD IEC 61000-4-2、IEC 61000-4-5、IEC 61000-4-4 SOT-23 ESD and Surge Protection (TVS/ESD) ROHS
C3760872 | Littelfuse | RXEF110 | -40℃~+85℃ 1.1A 1.5W 150mΩ 2.2A 380mΩ 40A 72V 8.2s Plugin Resettable Fuses ROHS
C144394 | JST | B3B-XH-A(LF)(SN) | -25℃~+85℃ 1 1x3P 2.5mm 250V 3 3A 3P 5.75mm 7mm 9.9mm Brass K Pin PA66 Through Hole Tin UL94V-0 White XH 插件,P=2.5mm Wire To Board Connector ROHS
C20079 | BOOMELE(Boom Precision Elec) | XH-2A | 1 1x2P 2 2.5mm 2P 5.8mm 7mm Through Hole White XH Plugin, P=2.5mm Wire To Board Connector ROHS
C57141 | BOOMELE(Boom Precision Elec) | XH-2AYellow | -25℃~+85℃ 1 1x2P 2 2.5mm 250V 2P 3A 5.8mm 7.5mm 7mm Through Hole XH Yellow Plugin, P=2.5mm Wire To Board Connector ROHS
C24192 | BOOMELE(Boom Precision Elec) | XH-2ARed | -25℃~+85℃ 1 1x2P 2 2.5mm 250V 2P 3A 5.8mm 7.5mm 7mm Red Through Hole XH Plugin, P=2.5mm Wire To Board Connector ROHS
C2316 | BOOMELE(Boom Precision Elec) | XH-3A | 1 10mm 1x3P 2.5mm 3 3P 5.8mm 7mm Through Hole White XH Plugin,P=2.5mm Wire To Board Connector ROHS
C37815 | BOOMELE(Boom Precision Elec) | XH-4A | 1 12.5mm 1x4P 2.5mm 4 4P 5.8mm 7mm Through Hole White XH Plugin, P=2.5mm Wire To Board Connector ROHS
C68117 | BOOMELE(Boom Precision Elec) | XH-4A Yellow | 1 1x4P 2.5mm 4 4P Through Hole XH Plugin,P=2.5mm Wire To Board Connector ROHS
C192885 | BOOMELE(Boom Precision Elec) | XH-4AGreen | 1 1x4P 2.5mm 4 4P Through Hole XH Plugin,P=2.5mm Wire To Board Connector ROHS
C57846 | BOOMELE(Boom Precision Elec) | XH-4ABlack | -25℃~+85℃ 1 12.5mm 1x4P 2.5mm 250V 3A 4 4P 5.8mm 7mm Black Through Hole XH Plugin,P=2.5mm Wire To Board Connector ROHS
C2318 | BOOMELE(Boom Precision Elec) | XH-5A | 1 15mm 1x5P 2.5mm 5 5.8mm 5P 7mm Through Hole White XH Plugin,P=2.5mm Wire To Board Connector ROHS
C57142 | BOOMELE(Boom Precision Elec) | XH-5ABlue | -25℃~+85℃ 1 15mm 1x5P 2.5mm 250V 3A 5 5.8mm 5P 7mm Blue Through Hole XH Plugin,P=2.5mm Wire To Board Connector ROHS
C5663 | BOOMELE(Boom Precision Elec) | XH-6A | 1 17.5mm 1x6P 2.5mm 5.8mm 6 6P 7mm Through Hole White XH Plugin,P=2.5mm Wire To Board Connector ROHS
C33435 | BOOMELE(Boom Precision Elec) | XH-9A | 1 1x9P 2.5mm 25mm 5.8mm 7mm 9 9P Through Hole White XH Plugin,P=2.5mm Wire To Board Connector ROHS
C16728 | BOOMELE(Boom Precision Elec) | VH-2A | -25℃~+85℃ 1 1x2P 2 250V 2P 3.96mm 5A Beige Brass PA66 Through Hole Tin UL94V-0 VH Plugin,P=3.96mm Wire To Board Connector ROHS
C8884 | BOOMELE(Boom Precision Elec) | VH-4A | -25℃~+85℃ 1 14mm 15.84mm 1x4P 250V 3.96mm 4 4P 5A Brass PA66 Through Hole Tin UL94V-0 VH White Plugin,P=3.96mm Wire To Board Connector ROHS
C21473 | BOOMELE(Boom Precision Elec) | VH-6A | -25℃~+85℃ 1 1x6P 250V 3.96mm 5A 6 6P Beige Brass PA66 Through Hole Tin UL94V-0 VH Plugin,P=3.96mm Wire To Board Connector ROHS
C48946905 | UMAX | PCIE-G4071141D | 42P 64P 7.4mm Clamping plate PCI-E 4.0 PCI-E x4 With post SMD PCI / PCIe Connector ROHS
C2718488 | BOOMELE(Boom Precision Elec) | 2.54-1*4PFemale | -40℃~+105℃ 1 1x4P 2.54mm 3A 4P Bronze Square Hole Through Hole Top Plugin,P=2.54mm Female Headers ROHS
C189677 | HANRUN(Zhongshan HanRun Elec) | HR981190C | Non-PoE RJ45 Jack Right Angle Shielded With Contact Spring With LED Plugin Ethernet Connectors / Modular Connectors (RJ45 RJ11) ROHS
C19725142 | USAKRO | DGUK611U2B101DB2WD | -40℃~+85℃ 2 Gold Non-PoE Phosphor bronze RJ45 Jack Right Angle Shielded With LED 插件 Ethernet Connectors / Modular Connectors (RJ45 RJ11) ROHS
C8410 | Ningbo Kangnex Elec | WJ15EDGVC-3.81-04P-14-00A | -40℃~+105℃ 1 1x4P 3.81mm 300V 4 4P 8A Board Side/Socket - Closed Green Hinged (Snap On) Through Hole Plugin,P=3.81mm Pluggable System Terminal Block ROHS
C601978 | JILN | 331010SG0ABLA02 | -40℃~+105℃ 2 2.54mm 2.54mm 2x5P 3A 5 Black Brass Gold IDC Header Through Hole Plugin,P=2.54mm IDC Connectors ROHS
C135264 | SXN(Shun Xiang Nuo Elec) | SMNR4030-220MT | 1.3A 1.3A 22uH 290mΩ Magnetic Shielded Inductor ±20% SMD, 4x4mm Power Inductors ROHS
C49073771 | COILANK INTERNATIONAL | AAPS0650M4R7H | 10A 30.8mΩ 4.7uH 6.5A ±20% SMD,6.6x6.4mm Power Inductors ROHS
C252941 | INGHAi | GMD12095YB-5V2400 | -20℃~+70℃ 12mm 2.4kHz 30mA 3V~7V 5V 7.6mm 85dB 9.5mm Active Buzzer (Built-in Driving Circuit) Electromagnetic Through-hole Plugin,D=12mm Buzzers ROHS
C21791 | Infineon Technologies | IRF7341TRPBF | -55℃~+150℃ 1V 2 N-Channel 2W 36nC 4.7A 50mΩ@10V 55V 71pF 740pF N-Channel SO-8 MOSFETs ROHS
C695267 | TOSHIBA | TK110P10PL,RQ(S2 | 1 N-channel 1.5V、2.5V 100V 2.04nF 22pF 310pF 33nC@10V 40A 75W 8.9mΩ@10V N-Channel TO-252-2(DPAK) MOSFETs ROHS
C141723 | TAI-TECH | FCM1608KF-601T03 | -55℃~+125℃ 1 350mA 500mΩ 600Ω@100MHz ±25% 0603 Ferrite Beads ROHS
C133937 | TAI-TECH | FCM1608KF-601T05 | 1 500mA 500mΩ 600Ω@100MHz ±25% 0603 Ferrite Beads ROHS
C466988 | Vishay Intertech | SI1902CDL-T1-GE3 | -55℃~+150℃ 1.1A 1.5V 2 N-Channel 20V 20pF 235mΩ@4.5V 420mW 62pF 7pF 900pC@4.5V N-Channel SC-70-6 MOSFETs ROHS
C82045 | onsemi | BSS138LT1G | -55℃~+150℃ 1 N-channel 200mA 225mW 5.6Ω@2.75V 500mV 50V 50pF 5pF SOT-23 MOSFETs ROHS
C844719 | Vishay Intertech | CRCW06030000Z0EAHP | -55℃~+155℃ 0Ω 333mW 75V Thick Film Resistor 0603 Chip Resistor - Surface Mount ROHS
C185338 | YAGEO | RC0603FR-0733K2L | -55℃~+155℃ 100mW 33.2kΩ 75V Thick Film Resistor ±1% ±100ppm/℃ 0603 Chip Resistor - Surface Mount ROHS
C14675 | YAGEO | RC0603FR-07100KL | -55℃~+155℃ 100kΩ 100mW 75V Thick Film Resistor ±1% ±100ppm/℃ 0603 Chip Resistor - Surface Mount ROHS
C861775 | YAGEO | RT0603BRE0724K9L | -55℃~+155℃ 100mW 24.9kΩ 75V Thin Film Resistor ±0.1% ±50ppm/℃ 0603 Chip Resistor - Surface Mount ROHS
C110776 | YAGEO | RT0603BRD071KL | -55℃~+155℃ 100mW 1kΩ 75V Thin Film Resistor ±0.1% ±25ppm/℃ 0603 Chip Resistor - Surface Mount ROHS
C138048 | YAGEO | RC0402FR-07174KL | -55℃~+155℃ 174kΩ 50V 62.5mW Thick Film Resistor ±1% ±100ppm/℃ 0402 Chip Resistor - Surface Mount ROHS
C295873 | YAGEO | RC0402FR-07118KL | -55℃~+155℃ 118kΩ 50V 62.5mW Thick Film Resistor ±1% ±100ppm/℃ 0402 Chip Resistor - Surface Mount ROHS
C852648 | YAGEO | RT0402BRD0722K1L | -55℃~+155℃ 22.1kΩ 50V 62.5mW Thin Film Resistor ±0.1% ±25ppm/℃ 0402 Chip Resistor - Surface Mount ROHS
C163478 | YAGEO | RC0402FR-0722K1L | -55℃~+155℃ 22.1kΩ 50V 62.5mW Thick Film Resistor ±1% ±100ppm/℃ 0402 Chip Resistor - Surface Mount ROHS
C105881 | YAGEO | RC0603FR-07330RL | -55℃~+155℃ 100mW 330Ω 75V Thick Film Resistor ±1% ±100ppm/℃ 0603 Chip Resistor - Surface Mount ROHS
C114670 | YAGEO | RC0603FR-07510RL | -55℃~+155℃ 100mW 510Ω 75V Thick Film Resistor ±1% ±100ppm/℃ 0603 Chip Resistor - Surface Mount ROHS
C174886 | Ever Ohms Tech | CR1812J33K0E04Z | -55℃~+155℃ 200V 33kΩ 750mW Thick Film Resistor ±100ppm/℃ ±5% 1812 Chip Resistor - Surface Mount ROHS
C98220 | YAGEO | RC0603FR-0710KL | -55℃~+155℃ 100mW 10kΩ 75V Thick Film Resistor ±1% ±100ppm/℃ 0603 Chip Resistor - Surface Mount ROHS
C171694 | YAGEO | RC0402FR-07309KL | -55℃~+155℃ 309kΩ 50V 62.5mW Thick Film Resistor ±1% ±100ppm/℃ 0402 Chip Resistor - Surface Mount ROHS
C859110 | YAGEO | RC0603FR-7W10KL | -55℃~+155℃ 10kΩ 200mW 75V Thick Film Resistor ±1% ±200ppm/℃ 0603 Chip Resistor - Surface Mount ROHS
C114759 | YAGEO | RC0402FR-071K5L | -55℃~+155℃ 1.5kΩ 50V 62.5mW Thick Film Resistor ±1% ±100ppm/℃ 0402 Chip Resistor - Surface Mount ROHS
C132157 | YAGEO | RC0402FR-0712K1L | -55℃~+155℃ 12.1kΩ 50V 62.5mW Thick Film Resistor ±1% ±100ppm/℃ 0402 Chip Resistor - Surface Mount ROHS
C138017 | YAGEO | RC0402FR-072K7L | -55℃~+155℃ 2.7kΩ 50V 62.5mW Thick Film Resistor ±1% ±100ppm/℃ 0402 Chip Resistor - Surface Mount ROHS
C87044 | YAGEO | RC0402FR-0749R9L | -55℃~+155℃ 49.9Ω 50V 62.5mW Thick Film Resistor ±1% ±100ppm/℃ 0402 Chip Resistor - Surface Mount ROHS
C137954 | YAGEO | RC0402FR-0760R4L | -55℃~+155℃ 50V 60.4Ω 62.5mW Thick Film Resistor ±1% ±100ppm/℃ 0402 Chip Resistor - Surface Mount ROHS
C137204 | YAGEO | RC1206JR-07120RL | -55℃~+155℃ 120Ω 200V 250mW Thick Film Resistor ±100ppm/℃ ±5% 1206 Chip Resistor - Surface Mount ROHS
C105579 | YAGEO | RC0603FR-0747KL | -55℃~+155℃ 100mW 47kΩ 75V Thick Film Resistor ±1% ±100ppm/℃ 0603 Chip Resistor - Surface Mount ROHS
C22427220 | Texas Instruments | LMR51610YDBVR | -40℃~+150℃@(TJ) 1 1.1MHz 1A 26.5uA 4V~65V 800mV~28V Adjustable Buck Buck Built-in Yes SOT-23-6 DC-DC Converters ROHS
C1855832 | Texas Instruments | LM61460AASQRJRRQ1 | -40℃~+150℃@(TJ) 1 2MHz 3V~36V 6A 6uA Adjustable Buck Buck Built-in Yes VQFN-14-HR(3.5x4) DC-DC Converters ROHS
C6186 | Advanced Monolithic Systems | AMS1117-3.3 | -40℃~+125℃ 0.003%Vout 1 1.1V@(800mA) 15V 1A 3.3V 5mA 72dB@(120Hz) Fixed Over Current Protection、Thermal Shutdown Positive SOT-223 Voltage Regulators - Linear, Low Drop Out (LDO) Regulators ROHS
C2832141 | Texas Instruments | LM66100DCKT | -40℃~+105℃ 1 1.5A 1.5V~5.5V 141mΩ Active Low Ideal Diode SC-70-6 Power Distribution Switches ROHS
C964636 | Texas Instruments | LSF0102DCUR | -40℃~+125℃ 1 1.8V~5.5V 2 950mV~4.5V Auto Direction Detection Bidirectional Push-Pull、Open Drain TTL TTL VSSOP-8-0.5mm Translators, Level Shifters ROHS
C71136 | UTC(Unisonic Tech) | 78L05G-AB3-R | -40℃~+85℃ 1 1.7V@(40mA) 100mA 2mA 30V 40uV 5V 80dB@(120Hz) Fixed Over Current Protection、Short Circuit Protection、Thermal Shutdown Positive SOT-89-3 Voltage Regulators - Linear, Low Drop Out (LDO) Regulators ROHS
C15219 | Analog Devices | ADUM1200ARZ-RL7 | -40℃~+125℃ 0 150ns 1Mbps 2 2.7V~5.5V 2.7V~5.5V 2500 25kV/us Bidirectional signal isolation、Multi-voltage domain interface、Power-on reset SOIC-8 Digital Isolators ROHS
C83775 | Microchip Tech | MCP1416T-E/OT | -40℃~+150℃ 1 1.5A 1.5A 20ns 20ns 4.5V~18V 650uA Low Side MOSFET SOT-23-5 Gate Drivers ROHS
C6489181 | Texas Instruments | SN74HCT245DGSR | -40℃~+85℃ 1 14ns@5.5V,50pF 4.5V~5.5V 6mA 6mA 74HCT 8 80uA Bidirectional Tri-State VSSOP-20 Buffers, Drivers, Receivers, Transceivers ROHS
C39693 | Terminus Tech | FE2.1-CQFP48A | 0℃~+70℃ 1.62V~1.98V、3V~3.6V、4.5V~5.5V 155mA 600uA USB 2.0 LQFP-48(7x7) USB Converters ROHS
C621425 | Microchip Tech | LAN8742AI-CZ-TR | -40℃~+85℃ 1.8V~3.3V LAN8742A Open Drain Schmitt trigger VQFN-24-EP(4x4) Buffers, Drivers, Receivers, Transceivers ROHS
C111212 | STMicroelectronics | USBLC6-4SC6 | -40℃~+125℃@(Tj) 10V 10nA 130W@8/20us 17V 3pF 5.25V 5A ESD Four channels IEC 61000-4-2 Unidirectional SOT-23-6L ESD and Surge Protection (TVS/ESD) ROHS
C3234119 | Texas Instruments | TCAN1044AVDRBRQ1 | -40℃~+150℃ 1.5uA 4.5V~5.5V 5Mbps 70mA CAN FD Transceiver SON-8(3x3) CAN Transceivers ROHS
C515584 | NXP Semicon | PCA9545APW,118 | -40℃~+85℃ 11Ω 2.3V~5.5V 300ps 4:1 I2C TSSOP-20 Analog Switches - Special Purpose ROHS
C23404 | Analog Devices Inc./Maxim Integrated | MAX3490EESA+T | -40℃~+85℃ 1 1 10Mbps 2.2mA 3V~3.6V Full-Duplex Transceiver ±15kV SOIC-8 RS-485 / RS-422 ICs ROHS
C9900005447 | CFSensor | XGZP6859DC100KPGPN | -100KPA to +100KPA, SMD-6, I2C
C2961106 | Avia Semicon (Xiamen) | HX717 | -40℃~+85℃ 1.5mA 10Hz、20Hz、80Hz、320Hz 2 2.7V~5.5V 24 3ppm/℃ External External、Built-in Serial port Support Yes SOP-16 Analog to Digital Converters (ADC) ROHS
C8142 | Texas Instruments | SN74LV4052APWR | -40℃~+85℃ 2V~5.5V 4 4:1 75Ω 7ns TSSOP-16 Analog Switches, Multiplexers ROHS
C3293138 | RENESAS | PS2801-1-F3-A/L | -55℃~+100℃ 1 1.1V 120mW 2.5kV 300mV@10mA,2mA 3us 50mA 50mA 5us 600% 6V 80% 80V DC Phototransistor SSOP-4-1.27mm Transistor, Photovoltaic Output Optoisolators ROHS
C5349954 | XINGLIGHT | XL-1615RGBC-2812B | -20℃~+85℃ 0.35mA 0.6mm 1.5mm 1.6mm 120° 130mcd、360mcd、110mcd 3.5V~5.5V 3000V 4.5kHz 800Kbit/s G:525nm、R:625nm、B:470nm R:620nm~625nm、B:465nm~470nm、G:525nm~530nm Top-mount Water Clear SMD-4P,1.6x1.5mm RGB LEDs(Built-in IC) ROHS
C7859 | Texas Instruments | SN74LVC4245APWR | -40℃~+85℃ 1 2.7V~3.6V 4.5V~5.5V 8 Bidirectional Tri-State TSSOP-24 Translators, Level Shifters ROHS
C6489181 | Texas Instruments | SN74HCT245DGSR | -40℃~+85℃ 1 14ns@5.5V,50pF 4.5V~5.5V 6mA 6mA 74HCT 8 80uA Bidirectional Tri-State VSSOP-20 Buffers, Drivers, Receivers, Transceivers ROHS
C524786 | Texas Instruments | AM26LV32IDR | -40℃~+85℃ 0 3.3V~3.6V 32Mbps 4 8mA Receiver ±5kV SOIC-16 RS-485 / RS-422 ICs ROHS
C843258 | NDK | NX2016SA-25MHZ-STD-CZS-2 | 25MHz 8pF Crystal Oscillator ±15ppm SMD2016-4P Crystals ROHS
C112573 | SMD5032-2P | X503212MSB2GI | -40℃~+85℃ 12MHz 20pF Crystal Oscillator ±10ppm ±20ppm SMD5032-2P Crystals ROHS
C697607 | Taiyo Yuden | HMK325C7475KN-TE | 4.7uF ±10% 100V Ceramic Capacitor X7S 1210
C2169715 | Taiyo Yuden | HMK107C7224KAHTE | 220nF ±10% 100V Ceramic Capacitor X7S 0603 AEC-Q200
C596323 | YAGEO | CC0805KKX7R0BB474 | 470nF ±10% 100V Ceramic Capacitor X7R 0805
C153291 | Samsung Electro-Mechanics | CL10B102KC8NNNC | 100V 1nF X7R ±10% 0603 Multilayer Ceramic Capacitors MLCC - SMD/SMT ROHS
C487184 | Ymin | VMML1652A221MV | 100V 12.5mm 16.5mm 220uF ±20% SMD,D12.5xL16.5mm Aluminum Electrolytic Capacitors - SMD ROHS
C88784 | Rubycon | 100PX220MEFC12.5X20 | -25℃~+105℃ 100V 12.5mm 2000hrs@105℃ 20mm 220uF 560mA@120Hz 5mm ±20% 插件,D12.5xL20mm Aluminum Electrolytic Capacitors - Leaded ROHS
C57895 | Samsung Electro-Mechanics | CL10A225KA8NNNC | 2.2uF 25V X5R ±10% 0603 Multilayer Ceramic Capacitors MLCC - SMD/SMT ROHS
C1623 | Samsung Electro-Mechanics | CL10B474KA8NNNC | 25V 470nF X7R ±10% 0603 Multilayer Ceramic Capacitors MLCC - SMD/SMT ROHS
C21122 | Samsung Electro-Mechanics | CL10B223KB8NNNC | 22nF 50V X7R ±10% 0603 Multilayer Ceramic Capacitors MLCC - SMD/SMT ROHS
C2764229 | JUSHUO | AFC20-S05BCA-00 | -20℃~+85℃ 1 13.9mm 1x5P 250V 2A 2mm 5 5.55mm 5P 7.55mm Beige Brass LCP PH Surface Mount,Vertical Tin UL94V-0 SMD,P=2mm Wire To Board Connector ROHS
C602033 | cjiang (Changjiang Microelectronics Tech) | FHD4020S-150MT | 1.2A 15uH 2.8A 305mΩ ±20% SMD,4x4mm Power Inductors ROHS
C534398 | Infineon Technologies | BSC098N10NS5 | -55℃~+150℃ 1 N-channel 100V 2.1nF 21pF 22nC@10V 3.8V 38A 69W 9.8mΩ@10V TDSON-8(5x6) MOSFETs ROHS
C107701 | YAGEO | RC0603FR-0722RL | -55℃~+155℃ 100mW 22Ω 75V Thick Film Resistor ±1% ±100ppm/℃ 0603 Chip Resistor - Surface Mount ROHS
C114623 | YAGEO | RC0603FR-0747RL | -55℃~+155℃ 100mW 47Ω 75V Thick Film Resistor ±1% ±100ppm/℃ 0603 Chip Resistor - Surface Mount ROHS
C2941097 | UNI-ROYAL(Uniroyal Elec) | LR123WF750MT4E | 3W 75mΩ Current Sense Resistor SMD ±1% ±50ppm/℃ 2512 Current Sense Resistors / Shunt Resistors ROHS
C112307 | YAGEO | RC0603FR-072R2L | -55℃~+155℃ 100mW 2.2Ω 75V Thick Film Resistor ±1% ±200ppm/℃ 0603 Chip Resistor - Surface Mount ROHS
C114669 | YAGEO | RC0603FR-07470RL | -55℃~+155℃ 100mW 470Ω 75V Thick Film Resistor ±1% ±100ppm/℃ 0603 Chip Resistor - Surface Mount ROHS
C112310 | YAGEO | RC0603FR-07680RL | -55℃~+155℃ 100mW 680Ω 75V Thick Film Resistor ±1% ±100ppm/℃ 0603 Chip Resistor - Surface Mount ROHS
C114662 | YAGEO | RC0603FR-072K2L | -55℃~+155℃ 100mW 2.2kΩ 75V Thick Film Resistor ±1% ±100ppm/℃ 0603 Chip Resistor - Surface Mount ROHS
C516354 | TRINAMIC Motion Control GmbH | TMC5160A-TA-T | -40℃~+125℃ 256 3.3V~5V 8V~60V Bipolar Driver No STEP/DIR、SPI、UART TQFP-48-EP(7x7) Stepper Motor Driver ROHS
C5216456 | Texas Instruments | ISO7762DWR | -55℃~+125℃ 100Mbps 100kV/us 11ns 2 2.25V~5.5V 2.25V~5.5V 4 5000 High Level SOIC-16 Digital Isolators ROHS
C5216395 | Texas Instruments | ISO6762DWR | -40℃~+125℃ 0 1.71V~1.89V 11ns 150kV/us 2.25V~5.5V 5000 50Mbps 6 High Level SOIC-16 Digital Isolators ROHS
C478459 | Texas Instruments | AM26C32IPWR | -40℃~+85℃ 0 10mA 4 4.5V~5.5V Receiver ±3kV TSSOP-16 RS-485 / RS-422 ICs ROHS
C41371861 | XFCN | XF-154 | Rectangular Bracket type 1 SMD Fuseholders RoHS
C3259897 | BOURNS | AV20K1210401NIR1 | 22V 400A Varistor Surface Mount 1210
C137001 | YAGEO | RC2512JK-073K3L | 1W 3.3kΩ 200V Thick Film Resistor ±100ppm/℃ ±5% 2512 Chip Resistor - Surface Mount RoHS
C193402 | MDD(Microdiode Semiconductor) | SMF5.0A | 9.2VC Clamp 21.7A@10/1000us Ipp TVS DIODE SOD-123FL

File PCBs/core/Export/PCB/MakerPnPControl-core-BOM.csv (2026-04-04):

# | RefDes | Quantity | Name | Value | Pattern | Manufacturer | MP | Package | Part Number (LCSC) | Part Number (Mouser) | Part Number (Digi-Key) | Datasheet | Number of Pins
1 | C1, C104, C105, C106, C107, C108, C109, C110, C112, C114, C115, C117, C119, C125, C128, C129, C131, C133, C134, C136, C137, C138, C139, C140, C141, C142, C143, C144, C145, C146, C147, C148, C149, C150, C151, C152, C153, C154, C155, C156, C158, C159, C301, C302, C303, C304, C402, C603, C604 | 49 | CAP_0402 | 100nF 6.3V 0402 | CAP_0402_MURATA |  |  |  |  |  |  |  | 2
2 | C2, C6, C10, C113 | 4 | CAP_0603 | 4.7uF 6.3V 0603 X5R 10% | CAP_0603_N | TDK |  |  |  |  |  | http://www.farnell.com/datasheets/2291921.pdf | 2
3 | C3, C7, C11, C116 | 4 | CAP_0402 | 200pF 16V 0402 X5R | CAP_0402_MURATA |  |  |  |  |  |  |  | 2
4 | C4, C5, C8, C9, C12, C13, C132, C160 | 8 | CAP_0805_N | 22uF 25V X5R | CAP_0805_N |  |  |  |  |  |  |  | 2
5 | C101, C126, C127, C130, C135 | 5 | CAP_0402 | 4.7uF 6.3V 0402 10% | CAP_0402_MURATA | Yageo |  |  |  |  |  |  | 2
6 | C102, C103, C111, C401 | 4 | CAP_0603 | 10uF 6.3V 0603 X5R 10% | CAP_0603_N | TDK |  |  |  |  |  | http://www.farnell.com/datasheets/2291921.pdf | 2
7 | C118, C120 | 2 | CAP_0603 | 10uF 6.3V 0603 X5R 20mOhm ESR 10% | CAP_0603_N | TDK |  |  |  |  |  | http://www.farnell.com/datasheets/2291921.pdf | 2
8 | C121, C122, C124 | 3 | CAP_0402 | 2.2uF 6.3V 0402 | CAP_0402_MURATA |  |  |  |  |  |  |  | 2
9 | C123, C157, C601, C602 | 4 | CAP_0402 | 1uF 6.3V 0402 | CAP_0402_MURATA | Murata |  |  |  |  |  | https://www.murata.com/~/media/webrenewal/support/library/catalog/products/capacitor/mlcc/c02e.ashx | 2
10 | D1 | 1 | LED 0603 BLUE | 3V3 | LED_0603_WURTH |  |  |  |  |  |  |  | 2
11 | D2 | 1 | LED 0603 BLUE | 3V3_ESP32 | LED_0603_WURTH |  |  |  |  |  |  |  | 2
12 | D101, D601, D602 | 3 | LED 0603 GREEN | CDONE | LED_0603_WURTH |  |  |  |  |  |  |  | 2
13 | D102 | 1 | BAV21W |  | SOD365X155X145L30X57N | MDD(Microdiode Semiconductor) |  |  | C113947 |  |  | https://www.lcsc.com/datasheet/C113947.pdf | 2
14 | D103 | 1 | LED 0603 RED | MCU_ACT | LED_0603_WURTH |  |  |  |  |  |  |  | 2
15 | D104 | 1 | LED 0603 ORANGE | ESP_ACT | LED_0603_WURTH |  |  |  |  |  |  |  | 2
16 | D105 | 1 | LED 0603 YELLOW | FPGA_ACT | LED_0603_WURTH |  |  |  |  |  |  |  | 2
17 | E1 | 1 | MDD_SMF5.0A | 5Vrwm '5.0' | MDD_SOD123FL_N | MDD(Microdiode Semiconductor) |  |  | C193402 |  |  | https://www.lcsc.com/datasheet/C193402.pdf | 2
18 | J1 | 1 | B2B-XH-A(LF)(SN) | AIN1 | SHDRV2W64P250_2X1_740X575H700 | JST |  |  | C158012 |  |  | http://datasheets.diptrace.com/jst/B11B-XH-A(LF)(SN)_and_series.pdf | 2
19 | J401 | 1 | PPTC041LFBN-RC | SWD | RHDRV4W80P254_4X1_1066X250H875_AP1 | Sullins |  |  |  |  | S7002-ND | http://datasheets.diptrace.com/con_headers/xPxCxxxLFBN-RC_10492-E.pdf | 4
20 | J402 | 1 | FTSH-105-01-X-DV-P-K-X | DEBUG | SAMTEC_FTSH-105-01-X-DV-P-K-X | Samtec | FTSH-105-01-F-DV-K |  |  |  |  |  | 10
21 | J403, J405, J408 | 3 | LPPB112NFSS-RC | LA2_IO | YXCON_F343-1211A0CMUB1 | Sullins |  |  |  |  | S9006E-11-ND | http://datasheets.diptrace.com/con_headers/LPPB__2NFSS-RC_11017-C.pdf | 22
22 | J404, J406, J409, J411 | 4 | 10164228-1001A1RLF |  | AMPHENOL_10164228-1001A1RLF | Amphenol ICC (FCI) |  |  |  |  |  | https://cdn.amphenol-cs.com/media/wysiwyg/files/drawing/10164227.pdf | 104
23 | J407 | 1 | PK-47309-375 |  | PK-47309-XXX | MOLEX |  |  |  |  |  | http://www.molex.com/pdm_docs/sd/473093351_sd.pdf | 12
24 | J410 | 1 | FTS-102-01-L-DV |  | SAMTEC_FTS-102-01-L-DV | Samtec |  |  |  |  | SAM1157-02-ND | http://datasheets.diptrace.com/con_headers/FTS-1XX-XX-XX-XX-XX-MKT.pdf | 4
25 | J601, J602 | 2 | TYPE-C 16PLT-H10.0 |  | TYPE-C 16PLT-H10.0 | SHOU HAN |  |  |  |  |  | https://datasheet.lcsc.com/lcsc/2206271801_SHOU-HAN-TYPE-C-16PLT-H10-0_C3151749.pdf | 22
26 | L1, L2, L3 | 3 | DFE252012F-1R0M | 1uH | IND_2520_N | Murata |  |  |  |  |  |  | 2
27 | L101 | 1 | IND_0603_N | 2.2uH 20% 1.8A 0.237ohm | IND_0603_TDK | TAIYO YUDEN |  |  |  |  |  |  | 2
28 | R1 | 1 | RES_1206_N | 0R 1206 | RES_1206_N |  |  |  |  |  |  |  | 2
29 | R2, R3 | 2 | RES_0402 | 220R 0402 1% | RES_0402_202305 |  |  |  |  |  |  |  | 2
30 | R4, R5, R101, R107, R109, R112, R113, R116, R117, R121, R122, R125, R128, R129, R131, R402, R404, R407, R408, R409, R605, R606, R608, R610 | 24 | RES_0402 | 10K 0402 1% | RES_0402_202305 |  |  |  |  |  |  |  | 2
31 | R6, R9, R10, R12, R13 | 5 | RES_0402 | 453K | RES_0402_202305 |  |  |  |  |  |  |  | 2
32 | R7, R8, R11, R14 | 4 | RES_0402 | 100K | RES_0402_202305 |  |  |  |  |  |  |  | 2
33 | R102, R103, R405, R406 | 4 | RES_0402 | 0R | RES_0402_202305 |  |  |  |  |  |  |  | 2
34 | R104 | 1 | RES_0402 | 47R | RES_0402_202305 |  |  |  |  |  |  |  | 2
35 | R105, R106, R134, R137, R138, R139, R611, R612 | 8 | RES_0402 | 330R 0402 1% | RES_0402_202305 |  |  |  |  |  |  |  | 2
36 | R108, R110, R111, R401 | 4 | RES_0603_N | 100R | RES_0603_N |  |  |  |  |  |  |  | 2
37 | R114, R115, R126, R127 | 4 | RES_0603_N | 1R 0603 | RES_0603_N |  |  |  |  |  |  |  | 2
38 | R118, R119, R120, R123, R124, R130, R132, R133, R135, R136 | 10 | RES_0402 | 33R 0402 1% | RES_0402_202305 |  |  |  |  |  |  |  | 2
39 | R403 | 1 | YC164-FR-072KL | 2K | RESCAXS8P80_320X160X70L30X50N | Yageo |  |  |  | 603-YC164-FR-072KL | YC164-FR-072KL-ND | http://datasheets.diptrace.com/rc_networks/PYu-YC_TC164_51_RoHS_L_3.pdf | 8
40 | R601, R602, R603, R604 | 4 | RES_0402 | 5K1 0402 1% | RES_0402_202305 |  |  |  |  |  |  |  | 2
41 | R607, R609 | 2 | RES_0402 | 4K7 0402 1% | RES_0402_202305 |  |  |  |  |  |  |  | 2
42 | S401 | 1 | TL1015 | H7_BOOT | TL1015 | E-SWITCH |  |  |  |  |  | https://www.e-switch.com/system/asset/product_line/data_sheet/142/TL1015.pdf | 2
43 | S402, S405, S406 | 3 | TL1015 | ESP_BOOT | TL1015 | E-SWITCH |  |  |  |  |  | https://www.e-switch.com/system/asset/product_line/data_sheet/142/TL1015.pdf | 2
44 | S403, S404 | 2 | TL1015 |  | TL1015 | E-SWITCH |  |  |  |  |  | https://www.e-switch.com/system/asset/product_line/data_sheet/142/TL1015.pdf | 2
45 | U1 | 1 | TPS3820-50DBVx |  | SOT23-5P95_280X145L45X40N_AD6 | Texas Instruments |  |  |  |  |  | http://datasheets.diptrace.com/ti/TPS3820-33DBVR_and_series.pdf | 5
46 | U2, U3, U4 | 3 | TPS62A02PDDCR |  | TI_DDC0006A_N | Texas Instruments |  |  | C22445521 |  |  | https://www.ti.com/lit/ds/symlink/tps62a02.pdf | 6
47 | U101 | 1 | STM32H725IxK_SPLIT |  | ST_UFBGA176+25_N | ST Microelectronics |  |  |  |  |  | https://www.st.com/resource/en/datasheet/stm32h725ae.pdf | 201
48 | U102 | 1 | ICE40HX8K-CT256 |  | LATTICE_caBGA256_N | Lattice Semiconductor | ICE40HX8K-CT256 | CABGA-256 Lattice Semiconductor |  |  |  |  | 256
49 | U103 | 1 | W25Q16JVUXIQ/W25Q16JVUXIM |  | USON-8_WINBOND | Winbond |  |  |  |  |  | https://www.winbond.com/resource-files/w25q16jv%20spi%20revh%2004082019%20plus.pdf | 9
50 | U104 | 1 | ESP32-C6-MINI-1-H4_SPLIT |  | XCVR_ESP32-C6-MINI-1-H4 | Espressif Systems | ESP32-C6-MINI-1-H4 | SMD-53 Espressif Systems |  |  |  |  | 61
51 | U301, U302, U303, U304 | 4 | SN3257QDYYRQ1 |  | TI_DYY0016A_N | Texas Instruments |  |  | C2875445 |  |  | https://www.ti.com/lit/ds/symlink/sn3257-q1.pdf | 16
52 | U601, U602 | 2 | TMUXHS221NKGR |  | NKG0010A | Texas Instruments |  |  | C7362468 |  |  | https://www.ti.com/lit/ds/symlink/tmuxhs221.pdf | 10
53 | Y101 | 1 | 8132H-50.000ML33DTL | 50Mhz HCMOS output | HCI_8132H_N | HCI |  |  | C19674255 |  |  | https://www.lcsc.com/datasheet/C19674255.pdf | 4
 |  | 206 |  |  |  |  |  |  |  |  |  |  | 1556

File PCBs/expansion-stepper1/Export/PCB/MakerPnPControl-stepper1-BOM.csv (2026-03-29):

# | RefDes | Quantity | Name | Value | Pattern | Manufacturer | MP | Package | Part Number (LCSC) | Part Number (Mouser) | Part Number (Digi-Key) | Datasheet | Number of Pins
1 | C1, C33 | 2 | CAP_1210_N | 4.7uF 100V 1210 X7R 20% | CAP_1210_N |  |  |  |  |  |  |  | 2
2 | C2, C3, C18, C19, C37, C38, C48, C49 | 8 | CAP_0603_N | 220nF 63V 0603 X5R 10% | CAP_0603_N |  |  |  |  |  |  |  | 2
3 | C4, C20, C39, C50 | 4 | CAP_0805_N | 470nF 63V 0805 X7R 10% | CAP_0805_N |  |  |  |  |  |  |  | 2
4 | C5, C7, C9, C21, C22, C24, C40, C41, C43, C51, C52, C54 | 12 | CAP_0603_N | 1nF 100V 0603 X7R 10% | CAP_0603_N |  |  |  |  |  |  |  | 2
5 | C6, C34 | 2 | CAP_0603_N | 100nF 63V 0603 X5R 10% | CAP_0603_N |  |  |  |  |  |  |  | 2
6 | C10, C12, C16, C25, C27, C44, C46, C55, C57 | 9 | VMML1652A221MV | 220uF 100V 20% | CAPAE1300X1650L475X115N_AD2 | Ymin |  |  | C487184 |  |  |  | 2
7 | C11, C15, C17, C26, C28, C45, C47, C56, C58 | 9 | 100PX220MEFC12.5X20 | 220uF 100V 20% | CAPPRD500W60D1350H2200 | Rubycon |  |  | C88784 |  |  | https://www.lcsc.com/datasheet/C88784.pdf | 2
8 | C13, C14, C35, C36 | 4 | CAP_0805_N | 22uF 25V 0805 X5R | CAP_0805_N |  |  |  |  |  |  |  | 2
9 | C23, C53 | 2 | CAP_0603_N | 100nF 25V 0603 X7R 10% | CAP_0603_N |  |  |  |  |  |  |  | 2
10 | C29, C30, C59, C60 | 4 | CAP_0603_N | 2.2uF 25V 0603 X5R 10% | CAP_0603_N |  |  |  |  |  |  |  | 2
11 | C31, C61 | 2 | CAP_0603_N | 470nF 16V 0603 X7R 10% | CAP_0603_N |  |  |  |  |  |  |  | 2
12 | C32, C62, C64, C66 | 4 | CAP_0603_N | 100nF 63V 0603 X7R 10% | CAP_0603_N |  |  |  |  |  |  |  | 2
13 | C63, C65 | 2 | CAP_0603_N | 22nF 100V 0603 X7R 10% | CAP_0603_N |  |  |  |  |  |  |  | 2
14 | C67, C68, C69, C70, C71, C72, C73, C74, C128, C129 | 10 | CAP_0603_N | 100nF 16V 0603 X7R 10% | CAP_0603_N |  |  |  |  |  |  |  | 2
15 | D1, D3 | 2 | LED 0603 GREEN | V5P0_B | LED_0603_WURTH |  |  |  |  |  |  |  | 2
16 | D2 | 1 | LED 0603 RED | V3P3_CPU | LED_0603_WURTH |  |  |  |  |  |  |  | 2
17 | D4, D5, D6, D7 | 4 | SMA-DO214A | 54Vclamp | DIOM510X266X229L115X145N |  |  |  |  |  |  |  | 2
18 | E1 | 1 | MDD_SMA_DO214AC_SMAJ5.0A | 5Vrwm 'AE' | DIOM510X266X229L115X145N | MDD(Microdiode Semiconductor) |  |  | C113952 |  |  |  | 2
19 | E2 | 1 | MDD_SMA_DO214AC_SMAJ7.0A | 12Vrwm 'AM' | DIOM510X266X229L115X145N | MDD(Microdiode Semiconductor) |  |  | C113957 |  |  |  | 2
20 | E5 | 1 | MDD_SMA_DO214AC_SMAJ48A | 48Vrwm 'CX' | DIOM510X266X229L115X145N | MDD(Microdiode Semiconductor) |  |  | C173502 |  |  | https://www.lcsc.com/datasheet/C89612.pdf | 2
21 | J1 | 1 | B4P-VH(LF)(SN) | M2 | JST_B4P-VH(LF)(SN) | JST | B4P-VH(LF)(SN) |  |  |  |  |  | 4
22 | J2 | 1 | B5B-PH-SM4-TB(LF)(SN) | ED1_B | JST_B5B-PH-SM4-TB | JST |  |  |  |  |  | http://datasheets.diptrace.com/jst/S2B-PH-K-S(LF)(SN)_and_series.pdf | 7
23 | J3 | 1 | B5B-PH-SM4-TB(LF)(SN) | ED2_B | JST_B5B-PH-SM4-TB | JST |  |  |  |  |  | http://datasheets.diptrace.com/jst/S2B-PH-K-S(LF)(SN)_and_series.pdf | 7
24 | J5 | 1 | B4P-VH(LF)(SN) | M1 | JST_B4P-VH(LF)(SN) | JST | B4P-VH(LF)(SN) |  |  |  |  |  | 4
25 | J6 | 1 | B2B-XH-A(LF)(SN) | FAN | SHDRV2W64P250_2X1_740X575H700 | JST |  |  | C158012 |  |  | http://datasheets.diptrace.com/jst/B11B-XH-A(LF)(SN)_and_series.pdf | 2
26 | J7 | 1 | B2P-VH(LF)(SN) | 48V | JST_B2P-VH(LF)(SN) | JST | B2P-VH(LF)(SN) |  |  |  |  |  | 2
27 | J23 | 1 | 2-2387405-2-CARD | Port_1 | 2387405-2-CARD | TE Connectivity |  |  |  |  |  | https://www.te.com/commerce/DocumentDelivery/DDEController?Action=srchrtrv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 | 64
28 | J35 | 1 | B9B-XH-A(LF)(SN) | ED1_A | SHDRV9W64P250_9X1_2490X575H700 | JST |  |  | C157966 |  |  | http://datasheets.diptrace.com/jst/B11B-XH-A(LF)(SN)_and_series.pdf | 9
29 | J36 | 1 | B9B-XH-A(LF)(SN) | ED2_A | SHDRV9W64P250_9X1_2490X575H700 | JST |  |  | C157966 |  |  | http://datasheets.diptrace.com/jst/B11B-XH-A(LF)(SN)_and_series.pdf | 9
30 | L1, L2 | 2 | FHD4020S-150MT | 15uH ~~2.5Asat | SUNLORD_4030S | Cjiang |  |  | C602033 |  |  | https://www.lcsc.com/datasheet/C602033.pdf | 2
31 | MH1, MH2 | 2 | Round |  | ROUND |  |  |  |  |  |  |  | 9
32 | Q1, Q3, Q5, Q6, Q8, Q10, Q12, Q15 | 8 | BSC098N10NS5 |  | IRF_PG-TDSON-8 | Infineon |  |  | C466988 |  |  | https://www.lcsc.com/datasheet/C534398.pdf | 5
33 | Q2, Q4, Q7, Q9, Q11, Q13, Q14, Q16 | 8 | BSC098N10NS5 | 2A -20V | IRF_PG-TDSON-8 | Infineon |  |  | C466988 |  |  | https://www.lcsc.com/datasheet/C534398.pdf | 5
34 | R1, R2, R3, R4, R10, R11, R12, R13, R35, R36, R37, R38, R42, R43, R44, R45 | 16 | RES_0603_N | 22R 1% 75V | RES_0603_N |  |  |  |  |  |  |  | 2
35 | R5, R6, R14, R15, R39, R40, R46, R47 | 8 | RES_0603_N | 47R 1% 75V | RES_0603_N |  |  |  |  |  |  |  | 2
36 | R7 | 1 | RES_0402 | 118K 0402 1% | RES_0402_202305 |  |  |  |  |  |  |  | 2
37 | R8, R34 | 2 | RES_0402 | 22K1 0402 1% | RES_0402_202305 |  |  |  |  |  |  |  | 2
38 | R9, R16, R41, R48, R57, R58, R59, R60 | 8 | RES_2512_N | 0R075 1206 1.5W 1% | RES_2512_N |  |  |  |  |  |  |  | 2
39 | R17, R49 | 2 | RES_0603_N | 2R2 | RES_0603_N |  |  |  |  |  |  |  | 2
40 | R18 | 1 | RES_0603_N | 470R | RES_0603_N |  |  |  |  |  |  |  | 2
41 | R19 | 1 | RES_0603_N | 680R | RES_0603_N |  |  |  |  |  |  |  | 2
42 | R20, R27, R28, R29, R30, R31 | 6 | RES_0603_N | 100K | RES_0603_N |  |  |  |  |  |  |  | 2
43 | R21, R22, R23, R24, R52, R53, R55, R56 | 8 | RES_0603_N | 10K | RES_0603_N |  |  |  |  |  |  |  | 2
44 | R25, R26, R32, R50, R51 | 5 | RES_0603_N | 0R | RES_0603_N |  |  |  |  |  |  |  | 2
45 | R33 | 1 | RES_0402 | 309K 0402 1% | RES_0402_202305 |  |  |  |  |  |  |  | 2
46 | R54 | 1 | RES_0603_N | 2K2 | RES_0603_N |  |  |  |  |  |  |  | 2
47 | R65 | 1 | RES_2512_N | 3K 1206 1W | RES_2512_N |  |  |  |  |  |  |  | 2
48 | R155, R156 | 2 | YC164-FR-072KL | 2K | RESCAXS8P80_320X160X70L30X50N | Yageo |  |  |  | 603-YC164-FR-072KL | YC164-FR-072KL-ND | http://datasheets.diptrace.com/rc_networks/PYu-YC_TC164_51_RoHS_L_3.pdf | 8
49 | RV1, RV2, RV3, RV4 | 4 | RES_1206_N | 1210 54Vclamp | RES_1210_N |  |  |  |  |  |  |  | 2
50 | U1, U3 | 2 | LMR51610YDBVR | 1100kHz PFM | SOT23-6P95_280X145L45X37N | Texas Instruments |  |  | C22427220 |  |  | https://www.ti.com/lit/ds/symlink/lmr51610.pdf | 6
51 | U2, U6 | 2 | TMC5160A-TA-T |  | TMC_TQFP48-EP_N | Trinamic |  |  |  |  |  | https://www.analog.com/media/en/technical-documentation/data-sheets/TMC5160A_datasheet_rev1.18.pdf | 49
52 | U4, U5, U7 | 3 | ISO6762DWR |  | SOIC16P127_1030X1030X265L83X41N_AD4 | Texas Instruments |  |  | C5216395 |  |  | https://www.ti.com/lit/ds/symlink/iso6760.pdf | 16
53 | U42, U43 | 2 | AM26C32IPWR |  | SOP16P65_500X640X120L62X24N_AD3 | Texas Instruments |  |  | C478459 |  |  | https://www.ti.com/lit/ds/symlink/am26c32.pdf | 16
54 | X2 | 1 | 01550900M |  | FUSE_01550900M | Littelfuse Inc. |  |  |  |  |  | https://www.lcsc.com/datasheet/C108518.pdf | 2
 |  | 190 |  |  |  |  |  |  |  |  |  |  | 716

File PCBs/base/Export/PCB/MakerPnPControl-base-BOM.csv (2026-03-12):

# | RefDes | Quantity | Name | Value | Pattern | Manufacturer | MP | Package | Part Number (LCSC) | Part Number (Mouser) | Part Number (Digi-Key) | Datasheet | Number of Pins
1 | C1, C2, C3, C7, C8, C41, C42 | 7 | UMK325B7475MMHT | 4.7uF 50V 1210 X7R 20% | CAP_1210_N | Taiyo Yuden |  |  |  |  |  |  | 2
2 | C4, C5, C9, C10 | 4 | GRM155R71H223KA12D | 22nF 50V 0402 X7R 20% | CAP_0402_N | Murata |  |  |  |  |  |  | 2
3 | C6, C15, C16, C43, C44 | 5 | CAP_0603_N | 100nF 63V 0603 X5R 10% | CAP_0603_N |  |  |  |  |  |  |  | 2
4 | C11, C12 | 2 | CAP_0603_N | 1uF 16V 0603 X7R | CAP_0603_N |  |  |  |  |  |  |  | 2
5 | C13, C14, C45, C46, C47, C48 | 6 | CAP_0805_N | 22uF 25V 0805 X5R | CAP_0805_N |  |  |  |  |  |  |  | 2
6 | C17, C18 | 2 | CAP_0603_N | 22pF 16V 0603 C0G 5% | CAP_0603_N |  |  |  |  |  |  |  | 2
7 | C19, C70, C71, C72, C78, C91, C97 | 7 | CAP_0603_N | 10uF 16V 0603 X5R 20% | CAP_0603_N |  |  |  |  |  |  |  | 2
8 | C20, C49, C50, C53, C54, C55, C56, C69, C87, C119, C124, C125, C126, C127, C128, C129, C130, C131, C132 | 19 | CAP_0603_N | 100nF 16V 0603 X7R 10% | CAP_0603_N | Samsung |  |  | C66501 |  |  |  | 2
9 | C21, C22, C23, C24, C25, C26, C28, C29 | 8 | CAP_1210 | 47uF 16V 1210 X7R | CAP_1210_N |  |  |  |  |  |  |  | 2
10 | C27 | 1 | CAPP_1206_N | 22uF 16V 1206 TANTALUM 20% | CAPP_1206_N |  |  |  |  |  |  |  | 2
11 | C30, C31, C32, C33 | 4 | VKME1651J331MV | 330uF 63V 20% | CAPAE1030X800L320X70N_AD2 | Ymin |  |  | C487393 |  |  | https://www.ymin.cn/chip-miniature-type-aluminum-electrolytic-capacitors-vkm-product/ | 2
12 | C34, C75, C76, C77, C81, C82, C83, C88, C89, C92, C93, C96 | 12 | CAP_0402 | 100nF 6.3V 0402 | RES_0402_202305 |  |  |  |  |  |  |  | 2
13 | C35, C38, C39 | 3 | 330uF 50V ±20% |  | CAPPRD500W60D1050H2200 | Nichicon |  |  | C2166065 |  |  | https://www.lcsc.com/datasheet/C2166065.pdf | 2
14 | C36, C37 | 2 | NEV220M63 |  | CAPPRD500W60D1050H2200 | NTE |  |  |  |  |  | http://datasheets.diptrace.com/nte/nev_neh.pdf | 2
15 | C40 | 1 | CAP_1812_N | 4.7nF 2kV 1812 | CAP_1812_N |  |  |  |  |  |  |  | 2
16 | C51, C52 | 2 | CAP_1206_N | 10uF 16V 1206 X7R | CAP_1206_N |  |  |  |  |  |  |  | 2
17 | C57, C58, C63, C64 | 4 | CAP_0402 | 100nF 25V 0402 X5R | RES_0402_202305 |  |  |  |  |  |  |  | 2
18 | C59, C60, C65, C66 | 4 | CAP_0603_N | 1uF 25V 0603 X5R | CAP_0603_N |  |  |  |  |  |  |  | 2
19 | C61, C62, C67, C68 | 4 | CAP_0603_N | 1nF 25V 0603 X5R | CAP_0603_N |  |  |  |  |  |  |  | 2
20 | C73 | 1 | CAP_0402 | 470pF 6.3V 0402 | RES_0402_202305 |  |  |  |  |  |  |  | 2
21 | C74 | 1 | CAP_0402 | 1uF 6.3V 0402 | RES_0402_202305 |  |  |  |  |  |  |  | 2
22 | C79, C80, C95 | 3 | CAP_0402 | 100nF 10V 0402 | RES_0402_202305 |  |  |  |  |  |  |  | 2
23 | C84, C85 | 2 | CAP_0402 | 4.7nF 100V 0402 X7R 10% | RES_0402_202305 |  | GRM155R72A472KA01D |  | C415704 |  |  | https://www.lcsc.com/datasheet/C415704.pdf | 2
24 | C86 | 1 | CAP_0603_N | 1uF 25V 0603 X7R 10% | CAP_0603_N | Samsung |  |  | C29936 |  |  |  | 2
25 | C90, C94, C120, C121, C122, C123 | 6 | CAP_0402 | 100nF 16V 0402 | RES_0402_202305 |  |  |  |  |  |  |  | 2
26 | C98, C99, C100, C102, C103, C104, C105, C106, C107, C108, C109, C110, C111, C112, C113, C114, C115, C116, C117, C118 | 20 | CAP_0603_N | 10nF 6.3V 0603 X5R 20% | CAP_0603_N |  |  |  |  |  |  |  | 2
27 | C101 | 1 | CAP_0603_N | 100nF 6.3V 0603 X5R 20% | CAP_0603_N |  |  |  |  |  |  |  | 2
28 | D1 | 1 | LED 0603 GREEN | V5P0_B | LED_0603_WURTH |  |  |  |  |  |  |  | 2
29 | D2 | 1 | LED 0603 RED | V3P3_CPU | LED_0603_WURTH |  |  |  |  |  |  |  | 2
30 | D3 | 1 | LED 0603 GREEN | V5P0_ISOLATED_1 | LED_0603_WURTH |  |  |  |  |  |  |  | 2
31 | D4 | 1 | LED 0603 GREEN | V5P0_A | LED_0603_WURTH |  |  |  |  |  |  |  | 2
32 | D5 | 1 | LED 0603 GREEN | V5P0_ISOLATED_2 | LED_0603_WURTH |  |  |  |  |  |  |  | 2
33 | D6 | 1 | LED 0603 WHITE | V7P0 | LED_0603_WURTH |  |  |  |  |  |  |  | 2
34 | D7, D8, D9, D10, D11, D12, D13, D16, D20, D21 | 10 | SS14 |  | DIOM529X267X242L114X150N | MDD(Microdiode Electronics) |  |  | C2480 |  |  | http://datasheets.diptrace.com/mdd/SS14.pdf | 2
35 | D14, D15, D17, D18 | 4 | SS310 |  | DIOM529X267X242L114X150N | FOSAN |  |  | C3014013 |  |  | https://www.lcsc.com/datasheet/C3014013.pdf | 2
36 | D19 | 1 | LED 0603 RED | V5P0_B | LED_0603_WURTH |  |  |  |  |  |  |  | 2
37 | E1 | 1 | MDD_SMA_DO214AC_SMAJ7.0A | 7Vrwm 'AM' | DIOM510X266X229L115X145N | MDD(Microdiode Semiconductor) |  |  | C138782 |  |  |  | 2
38 | E2, E3, E10, E11 | 4 | MDD_SMA_DO214AC_SMAJ5.0A | 5Vrwm 'AE' | DIOM510X266X229L115X145N | MDD(Microdiode Semiconductor) |  |  | C113952 |  |  |  | 2
39 | E4 | 1 | MDD_SMA_DO214AC_SMAJ24A | 24Vrwm 'BZ' | DIOM510X266X229L115X145N | MDD(Microdiode Semiconductor) |  |  | C113962 |  |  | https://www.lcsc.com/datasheet/C89612.pdf | 2
40 | E5, E6 | 2 | MDD_SMA_DO214AC_SMAJ48A | 48Vrwm 'CX' | DIOM510X266X229L115X145N | MDD(Microdiode Semiconductor) |  |  | C173502 |  |  | https://www.lcsc.com/datasheet/C89612.pdf | 2
41 | E7 | 1 | SMCJ6.0A-E3/57T | SMCJ6.0 | DIOM794X590X262L114X305N | VISHAY |  |  | C1976142 |  |  | https://www.lcsc.com/datasheet/C1976142.pdf | 2
42 | E8, E9 | 2 | MDD_SMA_DO214AC_SMAJ12A | 12Vrwm 'BE' | DIOM510X266X229L115X145N | MDD(Microdiode Semiconductor) |  |  | C113957 |  |  | https://jlcpcb.com/api/file/downloadByFileSystemAccessId/8588880447481135104 | 2
43 | E12, E13, E14, E15 | 4 | PESD5V0S2BT,215 |  | SOT23-3P95_230X110L30X43N | Philips/NXP |  |  | C49338 |  | 1727-3840-6-ND | http://datasheets.diptrace.com/philips-nxp/PESD5V0S2BT.pdf | 3
44 | F1, F2, F3, F4, F5, F6, F7, F8, F9, F10, F11, F12 | 12 | RXEF110 | XF110 | FUSRB508W52L1280T300H1750 | Littelfuse |  |  | C3760872 |  |  | https://jlcpcb.com/api/file/downloadByFileSystemAccessId/8589839246074159104 | 2
45 | J1 | 1 | B3B-XH-A(LF)(SN) | RGB_LED | SHDRV3W64P250_3X1_990X575H700 | JST |  |  | C144394 |  |  | http://datasheets.diptrace.com/jst/B11B-XH-A(LF)(SN)_and_series.pdf | 3
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

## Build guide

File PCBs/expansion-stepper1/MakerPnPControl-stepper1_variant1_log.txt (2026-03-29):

D:\Users\Hydra\Documents\dev\projects\makerpnp\makerpnp\target\release\variantbuilder_cli.exe @MakerPnPControl-stepper1_variant1.args
stores::eda_placements: Loading eda placements. source: Export/PCB/MakerPnPControl-stepper1-PnP.csv
variantbuilder_app: Loaded 190 placements
variantbuilder_app: excluding placements: ["C11", "C15", "C26", "C28", "C45", "C47", "C56", "C58", "C17", "J23", "MH1", "MH2", "D4", "D5", "D6", "D7"]
stores::substitutions: Loading eda substitutions. source: MakerPnPControl-stepper1_variant1_substitutions.csv
variantbuilder_app: Loaded 2 substitution rules from MakerPnPControl-stepper1_variant1_substitutions.csv
stores::substitutions: Loading eda substitutions. source: ../../global-substitutions.csv
variantbuilder_app: Loaded 121 substitution rules from ../../global-substitutions.csv
variantbuilder_app: disabling placements: []
stores::parts: Loading parts. source: ../../parts.csv
variantbuilder_app: Loaded 192 parts
stores::part_mappings: Loading part mappings. source: ../../part-mappings.csv
variantbuilder_app: Loaded 187 part mappings
variantbuilder_app: Loaded 0 load-out items
stores::assembly_rules: Loading assembly rules. source: MakerPnPControl-stepper1_variant1_rules.csv
variantbuilder_app: Loaded 1 assembly rules
variantbuilder_app: Assembly variant: Default
variantbuilder_app: Ref_des list:
variantbuilder_app: Matched 174 placements for assembly variant
variantbuilder_app: Mapping Result
├── C1 (name: 'CAP_1210_N', value: '4.7uF 100V 1210 X7R 20%')
│   └── manufacturer: 'Taiyo Yuden', mpn: 'HMK325C7475KN-TE' (Auto-selected)
├── C2 (name: 'CAP_0603_N', value: '220nF 63V 0603 X5R 10%')
│   └── Substituted (name: 'CAP_0603_N', value: '220nF 100V 0603 X5R 10%'), by (name_pattern: 'CAP_0603.*', value_pattern: '220nF 63V 0603 X5R 10%'), de-rate: 'from 63V to 100V'
│       └── manufacturer: 'Taiyo Yuden', mpn: 'HMK107C7224KAHTE' (Auto-selected)
├── C3 (name: 'CAP_0603_N', value: '220nF 63V 0603 X5R 10%')
│   └── Substituted (name: 'CAP_0603_N', value: '220nF 100V 0603 X5R 10%'), by (name_pattern: 'CAP_0603.*', value_pattern: '220nF 63V 0603 X5R 10%'), de-rate: 'from 63V to 100V'
│       └── manufacturer: 'Taiyo Yuden', mpn: 'HMK107C7224KAHTE' (Auto-selected)
├── C4 (name: 'CAP_0805_N', value: '470nF 63V 0805 X7R 10%')
│   └── manufacturer: 'YAGEO', mpn: 'CC0805KKX7R0BB474' (Auto-selected)
├── C5 (name: 'CAP_0603_N', value: '1nF 100V 0603 X7R 10%')
│   └── manufacturer: 'Samsung Electro-Mechanics', mpn: 'CL10B102KC8NNNC' (Auto-selected)
├── C6 (name: 'CAP_0603_N', value: '100nF 63V 0603 X5R 10%')
│   └── Substituted (name: 'CAP_0603_N', value: '100nF 100V 0603 X7R 10%'), by (name_pattern: 'CAP_0603_N', value_pattern: '100nF 63V 0603 X5R 10%'), de-rate: 'from 63V to 100V', de-rate: 'from X5R to X7R'
│       └── manufacturer: 'Samsung Electro-Mechanics', mpn: 'CL10B104KC8NNNC' (Auto-selected)
├── C7 (name: 'CAP_0603_N', value: '1nF 100V 0603 X7R 10%')
│   └── manufacturer: 'Samsung Electro-Mechanics', mpn: 'CL10B102KC8NNNC' (Auto-selected)
├── C9 (name: 'CAP_0603_N', value: '1nF 100V 0603 X7R 10%')
│   └── manufacturer: 'Samsung Electro-Mechanics', mpn: 'CL10B102KC8NNNC' (Auto-selected)
├── C10 (name: 'VMML1652A221MV', value: '220uF 100V 20%')
│   └── manufacturer: 'Ymin', mpn: 'VMML1652A221MV' (Auto-selected)
├── C12 (name: 'VMML1652A221MV', value: '220uF 100V 20%')
│   └── manufacturer: 'Ymin', mpn: 'VMML1652A221MV' (Auto-selected)
├── C13 (name: 'CAP_0805_N', value: '22uF 25V 0805 X5R')
│   └── Substituted (name: 'CAP_0805_N', value: '22uF 25V 0805 X5R 20%'), by (name_pattern: 'CAP_0805_N', value_pattern: '22uF 25V 0805 X5R'), comment: 'Use 20% by default'
│       └── manufacturer: 'Samsung Electro-Mechanics', mpn: 'CL10B104KB8NNNC' (Auto-selected)
├── C14 (name: 'CAP_0805_N', value: '22uF 25V 0805 X5R')
│   └── Substituted (name: 'CAP_0805_N', value: '22uF 25V 0805 X5R 20%'), by (name_pattern: 'CAP_0805_N', value_pattern: '22uF 25V 0805 X5R'), comment: 'Use 20% by default'
│       └── manufacturer: 'Samsung Electro-Mechanics', mpn: 'CL10B104KB8NNNC' (Auto-selected)
├── C16 (name: 'VMML1652A221MV', value: '220uF 100V 20%')
│   └── manufacturer: 'Ymin', mpn: 'VMML1652A221MV' (Auto-selected)
├── C18 (name: 'CAP_0603_N', value: '220nF 63V 0603 X5R 10%')
│   └── Substituted (name: 'CAP_0603_N', value: '220nF 100V 0603 X5R 10%'), by (name_pattern: 'CAP_0603.*', value_pattern: '220nF 63V 0603 X5R 10%'), de-rate: 'from 63V to 100V'
│       └── manufacturer: 'Taiyo Yuden', mpn: 'HMK107C7224KAHTE' (Auto-selected)
├── C19 (name: 'CAP_0603_N', value: '220nF 63V 0603 X5R 10%')
│   └── Substituted (name: 'CAP_0603_N', value: '220nF 100V 0603 X5R 10%'), by (name_pattern: 'CAP_0603.*', value_pattern: '220nF 63V 0603 X5R 10%'), de-rate: 'from 63V to 100V'
│       └── manufacturer: 'Taiyo Yuden', mpn: 'HMK107C7224KAHTE' (Auto-selected)
├── C20 (name: 'CAP_0805_N', value: '470nF 63V 0805 X7R 10%')
│   └── manufacturer: 'YAGEO', mpn: 'CC0805KKX7R0BB474' (Auto-selected)
├── C21 (name: 'CAP_0603_N', value: '1nF 100V 0603 X7R 10%')
│   └── manufacturer: 'Samsung Electro-Mechanics', mpn: 'CL10B102KC8NNNC' (Auto-selected)
├── C22 (name: 'CAP_0603_N', value: '1nF 100V 0603 X7R 10%')
│   └── manufacturer: 'Samsung Electro-Mechanics', mpn: 'CL10B102KC8NNNC' (Auto-selected)
├── C23 (name: 'CAP_0603_N', value: '100nF 25V 0603 X7R 10%')
│   └── Substituted (name: 'CAP_0603_N', value: '100nF 100V 0603 X7R 10%'), by (name_pattern: 'CAP_0603_N', value_pattern: '100nF 25V 0603 X7R 10%'), de-rate: 'from 25V to 100V'
│       └── manufacturer: 'Samsung Electro-Mechanics', mpn: 'CL10B104KC8NNNC' (Auto-selected)
├── C24 (name: 'CAP_0603_N', value: '1nF 100V 0603 X7R 10%')
│   └── manufacturer: 'Samsung Electro-Mechanics', mpn: 'CL10B102KC8NNNC' (Auto-selected)
├── C25 (name: 'VMML1652A221MV', value: '220uF 100V 20%')
│   └── manufacturer: 'Ymin', mpn: 'VMML1652A221MV' (Auto-selected)
├── C27 (name: 'VMML1652A221MV', value: '220uF 100V 20%')
│   └── manufacturer: 'Ymin', mpn: 'VMML1652A221MV' (Auto-selected)
├── C29 (name: 'CAP_0603_N', value: '2.2uF 25V 0603 X5R 10%')
│   └── manufacturer: 'Samsung Electro-Mechanics', mpn: 'CL10A225KA8NNNC' (Auto-selected)
├── C30 (name: 'CAP_0603_N', value: '2.2uF 25V 0603 X5R 10%')
│   └── manufacturer: 'Samsung Electro-Mechanics', mpn: 'CL10A225KA8NNNC' (Auto-selected)
├── C31 (name: 'CAP_0603_N', value: '470nF 16V 0603 X7R 10%')
│   └── manufacturer: 'Samsung Electro-Mechanics', mpn: 'CL10B474KA8NNNC' (Auto-selected)
├── C32 (name: 'CAP_0603_N', value: '100nF 63V 0603 X7R 10%')
│   └── Substituted (name: 'CAP_0603_N', value: '100nF 100V 0603 X7R 10%'), by (name_pattern: 'CAP_0603_N', value_pattern: '100nF 63V 0603 X7R 10%'), de-rate: 'from 63V to 100V'
│       └── manufacturer: 'Samsung Electro-Mechanics', mpn: 'CL10B104KC8NNNC' (Auto-selected)
├── C33 (name: 'CAP_1210_N', value: '4.7uF 100V 1210 X7R 20%')
│   └── manufacturer: 'Taiyo Yuden', mpn: 'HMK325C7475KN-TE' (Auto-selected)
├── C34 (name: 'CAP_0603_N', value: '100nF 63V 0603 X5R 10%')
│   └── Substituted (name: 'CAP_0603_N', value: '100nF 100V 0603 X7R 10%'), by (name_pattern: 'CAP_0603_N', value_pattern: '100nF 63V 0603 X5R 10%'), de-rate: 'from 63V to 100V', de-rate: 'from X5R to X7R'
│       └── manufacturer: 'Samsung Electro-Mechanics', mpn: 'CL10B104KC8NNNC' (Auto-selected)
├── C35 (name: 'CAP_0805_N', value: '22uF 25V 0805 X5R')
│   └── Substituted (name: 'CAP_0805_N', value: '22uF 25V 0805 X5R 20%'), by (name_pattern: 'CAP_0805_N', value_pattern: '22uF 25V 0805 X5R'), comment: 'Use 20% by default'
│       └── manufacturer: 'Samsung Electro-Mechanics', mpn: 'CL10B104KB8NNNC' (Auto-selected)
├── C36 (name: 'CAP_0805_N', value: '22uF 25V 0805 X5R')
│   └── Substituted (name: 'CAP_0805_N', value: '22uF 25V 0805 X5R 20%'), by (name_pattern: 'CAP_0805_N', value_pattern: '22uF 25V 0805 X5R'), comment: 'Use 20% by default'
│       └── manufacturer: 'Samsung Electro-Mechanics', mpn: 'CL10B104KB8NNNC' (Auto-selected)
├── C37 (name: 'CAP_0603_N', value: '220nF 63V 0603 X5R 10%')
│   └── Substituted (name: 'CAP_0603_N', value: '220nF 100V 0603 X5R 10%'), by (name_pattern: 'CAP_0603.*', value_pattern: '220nF 63V 0603 X5R 10%'), de-rate: 'from 63V to 100V'
│       └── manufacturer: 'Taiyo Yuden', mpn: 'HMK107C7224KAHTE' (Auto-selected)
├── C38 (name: 'CAP_0603_N', value: '220nF 63V 0603 X5R 10%')
│   └── Substituted (name: 'CAP_0603_N', value: '220nF 100V 0603 X5R 10%'), by (name_pattern: 'CAP_0603.*', value_pattern: '220nF 63V 0603 X5R 10%'), de-rate: 'from 63V to 100V'
│       └── manufacturer: 'Taiyo Yuden', mpn: 'HMK107C7224KAHTE' (Auto-selected)
├── C39 (name: 'CAP_0805_N', value: '470nF 63V 0805 X7R 10%')
│   └── manufacturer: 'YAGEO', mpn: 'CC0805KKX7R0BB474' (Auto-selected)
├── C40 (name: 'CAP_0603_N', value: '1nF 100V 0603 X7R 10%')
│   └── manufacturer: 'Samsung Electro-Mechanics', mpn: 'CL10B102KC8NNNC' (Auto-selected)
├── C41 (name: 'CAP_0603_N', value: '1nF 100V 0603 X7R 10%')
│   └── manufacturer: 'Samsung Electro-Mechanics', mpn: 'CL10B102KC8NNNC' (Auto-selected)
├── C43 (name: 'CAP_0603_N', value: '1nF 100V 0603 X7R 10%')
│   └── manufacturer: 'Samsung Electro-Mechanics', mpn: 'CL10B102KC8NNNC' (Auto-selected)
├── C44 (name: 'VMML1652A221MV', value: '220uF 100V 20%')
│   └── manufacturer: 'Ymin', mpn: 'VMML1652A221MV' (Auto-selected)
├── C46 (name: 'VMML1652A221MV', value: '220uF 100V 20%')
│   └── manufacturer: 'Ymin', mpn: 'VMML1652A221MV' (Auto-selected)
├── C48 (name: 'CAP_0603_N', value: '220nF 63V 0603 X5R 10%')
│   └── Substituted (name: 'CAP_0603_N', value: '220nF 100V 0603 X5R 10%'), by (name_pattern: 'CAP_0603.*', value_pattern: '220nF 63V 0603 X5R 10%'), de-rate: 'from 63V to 100V'
│       └── manufacturer: 'Taiyo Yuden', mpn: 'HMK107C7224KAHTE' (Auto-selected)
├── C49 (name: 'CAP_0603_N', value: '220nF 63V 0603 X5R 10%')
│   └── Substituted (name: 'CAP_0603_N', value: '220nF 100V 0603 X5R 10%'), by (name_pattern: 'CAP_0603.*', value_pattern: '220nF 63V 0603 X5R 10%'), de-rate: 'from 63V to 100V'
│       └── manufacturer: 'Taiyo Yuden', mpn: 'HMK107C7224KAHTE' (Auto-selected)
├── C50 (name: 'CAP_0805_N', value: '470nF 63V 0805 X7R 10%')
│   └── manufacturer: 'YAGEO', mpn: 'CC0805KKX7R0BB474' (Auto-selected)
├── C51 (name: 'CAP_0603_N', value: '1nF 100V 0603 X7R 10%')
│   └── manufacturer: 'Samsung Electro-Mechanics', mpn: 'CL10B102KC8NNNC' (Auto-selected)
├── C52 (name: 'CAP_0603_N', value: '1nF 100V 0603 X7R 10%')
│   └── manufacturer: 'Samsung Electro-Mechanics', mpn: 'CL10B102KC8NNNC' (Auto-selected)
├── C53 (name: 'CAP_0603_N', value: '100nF 25V 0603 X7R 10%')
│   └── Substituted (name: 'CAP_0603_N', value: '100nF 100V 0603 X7R 10%'), by (name_pattern: 'CAP_0603_N', value_pattern: '100nF 25V 0603 X7R 10%'), de-rate: 'from 25V to 100V'
│       └── manufacturer: 'Samsung Electro-Mechanics', mpn: 'CL10B104KC8NNNC' (Auto-selected)
├── C54 (name: 'CAP_0603_N', value: '1nF 100V 0603 X7R 10%')
│   └── manufacturer: 'Samsung Electro-Mechanics', mpn: 'CL10B102KC8NNNC' (Auto-selected)
├── C55 (name: 'VMML1652A221MV', value: '220uF 100V 20%')
│   └── manufacturer: 'Ymin', mpn: 'VMML1652A221MV' (Auto-selected)
├── C57 (name: 'VMML1652A221MV', value: '220uF 100V 20%')
│   └── manufacturer: 'Ymin', mpn: 'VMML1652A221MV' (Auto-selected)
├── C59 (name: 'CAP_0603_N', value: '2.2uF 25V 0603 X5R 10%')
│   └── manufacturer: 'Samsung Electro-Mechanics', mpn: 'CL10A225KA8NNNC' (Auto-selected)
├── C60 (name: 'CAP_0603_N', value: '2.2uF 25V 0603 X5R 10%')
│   └── manufacturer: 'Samsung Electro-Mechanics', mpn: 'CL10A225KA8NNNC' (Auto-selected)
├── C61 (name: 'CAP_0603_N', value: '470nF 16V 0603 X7R 10%')
│   └── manufacturer: 'Samsung Electro-Mechanics', mpn: 'CL10B474KA8NNNC' (Auto-selected)
├── C62 (name: 'CAP_0603_N', value: '100nF 63V 0603 X7R 10%')
│   └── Substituted (name: 'CAP_0603_N', value: '100nF 100V 0603 X7R 10%'), by (name_pattern: 'CAP_0603_N', value_pattern: '100nF 63V 0603 X7R 10%'), de-rate: 'from 63V to 100V'
│       └── manufacturer: 'Samsung Electro-Mechanics', mpn: 'CL10B104KC8NNNC' (Auto-selected)
├── C63 (name: 'CAP_0603_N', value: '22nF 100V 0603 X7R 10%')
│   └── manufacturer: 'Samsung Electro-Mechanics', mpn: 'CL10B223KB8NNNC' (Auto-selected)
├── C64 (name: 'CAP_0603_N', value: '100nF 63V 0603 X7R 10%')
│   └── Substituted (name: 'CAP_0603_N', value: '100nF 100V 0603 X7R 10%'), by (name_pattern: 'CAP_0603_N', value_pattern: '100nF 63V 0603 X7R 10%'), de-rate: 'from 63V to 100V'
│       └── manufacturer: 'Samsung Electro-Mechanics', mpn: 'CL10B104KC8NNNC' (Auto-selected)
├── C65 (name: 'CAP_0603_N', value: '22nF 100V 0603 X7R 10%')
│   └── manufacturer: 'Samsung Electro-Mechanics', mpn: 'CL10B223KB8NNNC' (Auto-selected)
├── C66 (name: 'CAP_0603_N', value: '100nF 63V 0603 X7R 10%')
│   └── Substituted (name: 'CAP_0603_N', value: '100nF 100V 0603 X7R 10%'), by (name_pattern: 'CAP_0603_N', value_pattern: '100nF 63V 0603 X7R 10%'), de-rate: 'from 63V to 100V'
│       └── manufacturer: 'Samsung Electro-Mechanics', mpn: 'CL10B104KC8NNNC' (Auto-selected)
├── C67 (name: 'CAP_0603_N', value: '100nF 16V 0603 X7R 10%')
│   └── Substituted (name: 'CAP_0603_N', value: '100nF 100V 0603 X7R 10%'), by (name_pattern: 'CAP_0603_N', value_pattern: '100nF 16V 0603 X7R 10%'), de-rate: 'from 16V to 100V'
│       └── manufacturer: 'Samsung Electro-Mechanics', mpn: 'CL10B104KC8NNNC' (Auto-selected)
├── C68 (name: 'CAP_0603_N', value: '100nF 16V 0603 X7R 10%')
│   └── Substituted (name: 'CAP_0603_N', value: '100nF 100V 0603 X7R 10%'), by (name_pattern: 'CAP_0603_N', value_pattern: '100nF 16V 0603 X7R 10%'), de-rate: 'from 16V to 100V'
│       └── manufacturer: 'Samsung Electro-Mechanics', mpn: 'CL10B104KC8NNNC' (Auto-selected)
├── C69 (name: 'CAP_0603_N', value: '100nF 16V 0603 X7R 10%')
│   └── Substituted (name: 'CAP_0603_N', value: '100nF 100V 0603 X7R 10%'), by (name_pattern: 'CAP_0603_N', value_pattern: '100nF 16V 0603 X7R 10%'), de-rate: 'from 16V to 100V'
│       └── manufacturer: 'Samsung Electro-Mechanics', mpn: 'CL10B104KC8NNNC' (Auto-selected)
├── C70 (name: 'CAP_0603_N', value: '100nF 16V 0603 X7R 10%')
│   └── Substituted (name: 'CAP_0603_N', value: '100nF 100V 0603 X7R 10%'), by (name_pattern: 'CAP_0603_N', value_pattern: '100nF 16V 0603 X7R 10%'), de-rate: 'from 16V to 100V'
│       └── manufacturer: 'Samsung Electro-Mechanics', mpn: 'CL10B104KC8NNNC' (Auto-selected)
├── C71 (name: 'CAP_0603_N', value: '100nF 16V 0603 X7R 10%')
│   └── Substituted (name: 'CAP_0603_N', value: '100nF 100V 0603 X7R 10%'), by (name_pattern: 'CAP_0603_N', value_pattern: '100nF 16V 0603 X7R 10%'), de-rate: 'from 16V to 100V'
│       └── manufacturer: 'Samsung Electro-Mechanics', mpn: 'CL10B104KC8NNNC' (Auto-selected)
├── C72 (name: 'CAP_0603_N', value: '100nF 16V 0603 X7R 10%')
│   └── Substituted (name: 'CAP_0603_N', value: '100nF 100V 0603 X7R 10%'), by (name_pattern: 'CAP_0603_N', value_pattern: '100nF 16V 0603 X7R 10%'), de-rate: 'from 16V to 100V'
│       └── manufacturer: 'Samsung Electro-Mechanics', mpn: 'CL10B104KC8NNNC' (Auto-selected)
├── C73 (name: 'CAP_0603_N', value: '100nF 16V 0603 X7R 10%')
│   └── Substituted (name: 'CAP_0603_N', value: '100nF 100V 0603 X7R 10%'), by (name_pattern: 'CAP_0603_N', value_pattern: '100nF 16V 0603 X7R 10%'), de-rate: 'from 16V to 100V'
│       └── manufacturer: 'Samsung Electro-Mechanics', mpn: 'CL10B104KC8NNNC' (Auto-selected)
├── C74 (name: 'CAP_0603_N', value: '100nF 16V 0603 X7R 10%')
│   └── Substituted (name: 'CAP_0603_N', value: '100nF 100V 0603 X7R 10%'), by (name_pattern: 'CAP_0603_N', value_pattern: '100nF 16V 0603 X7R 10%'), de-rate: 'from 16V to 100V'
│       └── manufacturer: 'Samsung Electro-Mechanics', mpn: 'CL10B104KC8NNNC' (Auto-selected)
├── C128 (name: 'CAP_0603_N', value: '100nF 16V 0603 X7R 10%')
│   └── Substituted (name: 'CAP_0603_N', value: '100nF 100V 0603 X7R 10%'), by (name_pattern: 'CAP_0603_N', value_pattern: '100nF 16V 0603 X7R 10%'), de-rate: 'from 16V to 100V'
│       └── manufacturer: 'Samsung Electro-Mechanics', mpn: 'CL10B104KC8NNNC' (Auto-selected)
├── C129 (name: 'CAP_0603_N', value: '100nF 16V 0603 X7R 10%')
│   └── Substituted (name: 'CAP_0603_N', value: '100nF 100V 0603 X7R 10%'), by (name_pattern: 'CAP_0603_N', value_pattern: '100nF 16V 0603 X7R 10%'), de-rate: 'from 16V to 100V'
│       └── manufacturer: 'Samsung Electro-Mechanics', mpn: 'CL10B104KC8NNNC' (Auto-selected)
├── D1 (name: 'LED 0603 GREEN', value: 'V5P0_B')
│   └── Substituted (name: 'LED_0603', value: 'GREEN'), by (name_pattern: 'LED 0603 GREEN', value_pattern: '.*'), comment: ''
│       └── manufacturer: 'Foshan NationStar Optoelectronics', mpn: 'NCD0603G1' (Auto-selected)
├── D2 (name: 'LED 0603 RED', value: 'V3P3_CPU')
│   └── Substituted (name: 'LED_0603', value: 'RED'), by (name_pattern: 'LED 0603 RED', value_pattern: '.*'), comment: ''
│       └── manufacturer: 'Foshan NationStar Optoelectronics', mpn: 'NCD0603R5' (Auto-selected)
├── D3 (name: 'LED 0603 GREEN', value: 'V5P0_B')
│   └── Substituted (name: 'LED_0603', value: 'GREEN'), by (name_pattern: 'LED 0603 GREEN', value_pattern: '.*'), comment: ''
│       └── manufacturer: 'Foshan NationStar Optoelectronics', mpn: 'NCD0603G1' (Auto-selected)
├── E1 (name: 'MDD_SMA_DO214AC_SMAJ5.0A', value: '5Vrwm 'AE'')
│   └── manufacturer: 'MDD(Microdiode Semiconductor)', mpn: 'SMAJ5.0A' (Auto-selected)
├── E2 (name: 'MDD_SMA_DO214AC_SMAJ7.0A', value: '12Vrwm 'AM'')
│   └── manufacturer: 'MDD(Microdiode Semiconductor)', mpn: 'SMAJ7.0A' (Auto-selected)
├── E5 (name: 'MDD_SMA_DO214AC_SMAJ48A', value: '48Vrwm 'CX'')
│   ├── manufacturer: 'STMicroelectronics', mpn: 'SMAJ48A-TR' (Matched assembly-rule)
│   └── manufacturer: 'MDD(Microdiode Semiconductor)', mpn: 'SMAJ48A'
├── J1 (name: 'B4P-VH(LF)(SN)', value: 'M2')
│   └── Substituted (name: 'VH-4A', value: ''), by (name_pattern: 'B4P-VH(LF)(SN)', value_pattern: '.*'), comment: 'Use BOOMELE brand'
│       └── manufacturer: 'BOOMELE(Boom Precision Elec)', mpn: 'VH-4A' (Auto-selected)
├── J2 (name: 'B5B-PH-SM4-TB(LF)(SN)', value: 'ED1_B')
│   └── Substituted (name: 'AFC20-S05BCA-00', value: ''), by (name_pattern: 'B5B-PH-SM4-TB(LF)(SN)', value_pattern: '.*'), comment: 'Use JUSHO brand'
│       └── manufacturer: 'JUSHUO', mpn: 'AFC20-S05BCA-00' (Auto-selected)
├── J3 (name: 'B5B-PH-SM4-TB(LF)(SN)', value: 'ED2_B')
│   └── Substituted (name: 'AFC20-S05BCA-00', value: ''), by (name_pattern: 'B5B-PH-SM4-TB(LF)(SN)', value_pattern: '.*'), comment: 'Use JUSHO brand'
│       └── manufacturer: 'JUSHUO', mpn: 'AFC20-S05BCA-00' (Auto-selected)
├── J5 (name: 'B4P-VH(LF)(SN)', value: 'M1')
│   └── Substituted (name: 'VH-4A', value: ''), by (name_pattern: 'B4P-VH(LF)(SN)', value_pattern: '.*'), comment: 'Use BOOMELE brand'
│       └── manufacturer: 'BOOMELE(Boom Precision Elec)', mpn: 'VH-4A' (Auto-selected)
├── J6 (name: 'B2B-XH-A(LF)(SN)', value: 'FAN')
│   └── Substituted (name: 'GT-A2501WVD-102SBT01', value: ''), by (name_pattern: 'B2B-XH-A(LF)(SN)', value_pattern: '.*'), comment: 'Use g-switch brand instead'
│       └── manufacturer: 'G-Switch', mpn: 'GT-A2501WVD-102SBT01' (Auto-selected)
├── J7 (name: 'B2P-VH(LF)(SN)', value: '48V')
│   └── Substituted (name: 'VH-2A', value: ''), by (name_pattern: 'B2P-VH(LF)(SN)', value_pattern: '.*'), comment: 'Use BOOMELE brand'
│       └── manufacturer: 'BOOMELE(Boom Precision Elec)', mpn: 'VH-2A' (Auto-selected)
├── J35 (name: 'B9B-XH-A(LF)(SN)', value: 'ED1_A')
│   └── Substituted (name: 'XH-9A', value: ''), by (name_pattern: 'B9B-XH-A(LF)(SN)', value_pattern: '.*'), comment: 'Use BOOMELE brand'
│       └── manufacturer: 'BOOMELE(Boom Precision Elec)', mpn: 'XH-9A' (Auto-selected)
├── J36 (name: 'B9B-XH-A(LF)(SN)', value: 'ED2_A')
│   └── Substituted (name: 'XH-9A', value: ''), by (name_pattern: 'B9B-XH-A(LF)(SN)', value_pattern: '.*'), comment: 'Use BOOMELE brand'
│       └── manufacturer: 'BOOMELE(Boom Precision Elec)', mpn: 'XH-9A' (Auto-selected)
├── L1 (name: 'FHD4020S-150MT', value: '15uH ~~2.5Asat')
│   └── manufacturer: 'cjiang (Changjiang Microelectronics Tech)', mpn: 'FHD4020S-150MT' (Auto-selected)
├── L2 (name: 'FHD4020S-150MT', value: '15uH ~~2.5Asat')
│   └── manufacturer: 'cjiang (Changjiang Microelectronics Tech)', mpn: 'FHD4020S-150MT' (Auto-selected)
├── Q1 (name: 'BSC098N10NS5', value: '')
│   └── manufacturer: 'Infineon Technologies', mpn: 'BSC098N10NS5' (Auto-selected)
├── Q2 (name: 'BSC098N10NS5', value: '2A -20V')
│   └── manufacturer: 'Infineon Technologies', mpn: 'BSC098N10NS5' (Auto-selected)
├── Q3 (name: 'BSC098N10NS5', value: '')
│   └── manufacturer: 'Infineon Technologies', mpn: 'BSC098N10NS5' (Auto-selected)
├── Q4 (name: 'BSC098N10NS5', value: '2A -20V')
│   └── manufacturer: 'Infineon Technologies', mpn: 'BSC098N10NS5' (Auto-selected)
├── Q5 (name: 'BSC098N10NS5', value: '')
│   └── manufacturer: 'Infineon Technologies', mpn: 'BSC098N10NS5' (Auto-selected)
├── Q6 (name: 'BSC098N10NS5', value: '')
│   └── manufacturer: 'Infineon Technologies', mpn: 'BSC098N10NS5' (Auto-selected)
├── Q7 (name: 'BSC098N10NS5', value: '2A -20V')
│   └── manufacturer: 'Infineon Technologies', mpn: 'BSC098N10NS5' (Auto-selected)
├── Q8 (name: 'BSC098N10NS5', value: '')
│   └── manufacturer: 'Infineon Technologies', mpn: 'BSC098N10NS5' (Auto-selected)
├── Q9 (name: 'BSC098N10NS5', value: '2A -20V')
│   └── manufacturer: 'Infineon Technologies', mpn: 'BSC098N10NS5' (Auto-selected)
├── Q10 (name: 'BSC098N10NS5', value: '')
│   └── manufacturer: 'Infineon Technologies', mpn: 'BSC098N10NS5' (Auto-selected)
├── Q11 (name: 'BSC098N10NS5', value: '2A -20V')
│   └── manufacturer: 'Infineon Technologies', mpn: 'BSC098N10NS5' (Auto-selected)
├── Q12 (name: 'BSC098N10NS5', value: '')
│   └── manufacturer: 'Infineon Technologies', mpn: 'BSC098N10NS5' (Auto-selected)
├── Q13 (name: 'BSC098N10NS5', value: '2A -20V')
│   └── manufacturer: 'Infineon Technologies', mpn: 'BSC098N10NS5' (Auto-selected)
├── Q14 (name: 'BSC098N10NS5', value: '2A -20V')
│   └── manufacturer: 'Infineon Technologies', mpn: 'BSC098N10NS5' (Auto-selected)
├── Q15 (name: 'BSC098N10NS5', value: '')
│   └── manufacturer: 'Infineon Technologies', mpn: 'BSC098N10NS5' (Auto-selected)
├── Q16 (name: 'BSC098N10NS5', value: '2A -20V')
│   └── manufacturer: 'Infineon Technologies', mpn: 'BSC098N10NS5' (Auto-selected)
├── R1 (name: 'RES_0603_N', value: '22R 1% 75V')
│   └── Substituted (name: 'RES_0603_N', value: '22R 0603 1% 75V 100mW'), by (name_pattern: 'RES_0603.*', value_pattern: '22R 1% 75V'), comment: 'Add size code', comment: 'Use 100mW by default'
│       └── manufacturer: 'YAGEO', mpn: 'RC0603FR-0722RL' (Auto-selected)
├── R2 (name: 'RES_0603_N', value: '22R 1% 75V')
│   └── Substituted (name: 'RES_0603_N', value: '22R 0603 1% 75V 100mW'), by (name_pattern: 'RES_0603.*', value_pattern: '22R 1% 75V'), comment: 'Add size code', comment: 'Use 100mW by default'
│       └── manufacturer: 'YAGEO', mpn: 'RC0603FR-0722RL' (Auto-selected)
├── R3 (name: 'RES_0603_N', value: '22R 1% 75V')
│   └── Substituted (name: 'RES_0603_N', value: '22R 0603 1% 75V 100mW'), by (name_pattern: 'RES_0603.*', value_pattern: '22R 1% 75V'), comment: 'Add size code', comment: 'Use 100mW by default'
│       └── manufacturer: 'YAGEO', mpn: 'RC0603FR-0722RL' (Auto-selected)
├── R4 (name: 'RES_0603_N', value: '22R 1% 75V')
│   └── Substituted (name: 'RES_0603_N', value: '22R 0603 1% 75V 100mW'), by (name_pattern: 'RES_0603.*', value_pattern: '22R 1% 75V'), comment: 'Add size code', comment: 'Use 100mW by default'
│       └── manufacturer: 'YAGEO', mpn: 'RC0603FR-0722RL' (Auto-selected)
├── R5 (name: 'RES_0603_N', value: '47R 1% 75V')
│   └── Substituted (name: 'RES_0603_N', value: '47R 0603 1% 75V 100mW'), by (name_pattern: 'RES_0603.*', value_pattern: '47R 1% 75V'), comment: 'Add size code', comment: 'Use 100mW by default'
│       └── manufacturer: 'YAGEO', mpn: 'RC0603FR-0747RL' (Auto-selected)
├── R6 (name: 'RES_0603_N', value: '47R 1% 75V')
│   └── Substituted (name: 'RES_0603_N', value: '47R 0603 1% 75V 100mW'), by (name_pattern: 'RES_0603.*', value_pattern: '47R 1% 75V'), comment: 'Add size code', comment: 'Use 100mW by default'
│       └── manufacturer: 'YAGEO', mpn: 'RC0603FR-0747RL' (Auto-selected)
├── R7 (name: 'RES_0402', value: '118K 0402 1%')
│   └── Substituted (name: 'RES_0402', value: '118K 0402 1% 50V 62.5mW'), by (name_pattern: 'RES_0402', value_pattern: '118K 0402 1%'), comment: 'Use 50V by default', comment: 'Use 62.5mW by default'
│       └── manufacturer: 'YAGEO', mpn: 'RC0402FR-07118KL' (Auto-selected)
├── R8 (name: 'RES_0402', value: '22K1 0402 1%')
│   └── Substituted (name: 'RES_0402', value: '22K1 0402 1% 50V 62.5mW'), by (name_pattern: 'RES_0402', value_pattern: '22K1 0402 1%'), comment: 'Use 50V by default', comment: 'Use 62.5mW by default'
│       └── manufacturer: 'YAGEO', mpn: 'RC0402FR-0722K1L' (Auto-selected)
├── R9 (name: 'RES_2512_N', value: '0R075 1206 1.5W 1%')
│   └── Substituted (name: 'RES_2512_N', value: '0R075 1206 3W 1%'), by (name_pattern: 'RES_2512.*', value_pattern: '0R075 1206 1.5W 1%'), de-rate: 'from 1.5W to 3W'
│       └── manufacturer: 'UNI-ROYAL(Uniroyal Elec)', mpn: 'LR123WF750MT4E' (Auto-selected)
├── R10 (name: 'RES_0603_N', value: '22R 1% 75V')
│   └── Substituted (name: 'RES_0603_N', value: '22R 0603 1% 75V 100mW'), by (name_pattern: 'RES_0603.*', value_pattern: '22R 1% 75V'), comment: 'Add size code', comment: 'Use 100mW by default'
│       └── manufacturer: 'YAGEO', mpn: 'RC0603FR-0722RL' (Auto-selected)
├── R11 (name: 'RES_0603_N', value: '22R 1% 75V')
│   └── Substituted (name: 'RES_0603_N', value: '22R 0603 1% 75V 100mW'), by (name_pattern: 'RES_0603.*', value_pattern: '22R 1% 75V'), comment: 'Add size code', comment: 'Use 100mW by default'
│       └── manufacturer: 'YAGEO', mpn: 'RC0603FR-0722RL' (Auto-selected)
├── R12 (name: 'RES_0603_N', value: '22R 1% 75V')
│   └── Substituted (name: 'RES_0603_N', value: '22R 0603 1% 75V 100mW'), by (name_pattern: 'RES_0603.*', value_pattern: '22R 1% 75V'), comment: 'Add size code', comment: 'Use 100mW by default'
│       └── manufacturer: 'YAGEO', mpn: 'RC0603FR-0722RL' (Auto-selected)
├── R13 (name: 'RES_0603_N', value: '22R 1% 75V')
│   └── Substituted (name: 'RES_0603_N', value: '22R 0603 1% 75V 100mW'), by (name_pattern: 'RES_0603.*', value_pattern: '22R 1% 75V'), comment: 'Add size code', comment: 'Use 100mW by default'
│       └── manufacturer: 'YAGEO', mpn: 'RC0603FR-0722RL' (Auto-selected)
├── R14 (name: 'RES_0603_N', value: '47R 1% 75V')
│   └── Substituted (name: 'RES_0603_N', value: '47R 0603 1% 75V 100mW'), by (name_pattern: 'RES_0603.*', value_pattern: '47R 1% 75V'), comment: 'Add size code', comment: 'Use 100mW by default'
│       └── manufacturer: 'YAGEO', mpn: 'RC0603FR-0747RL' (Auto-selected)
├── R15 (name: 'RES_0603_N', value: '47R 1% 75V')
│   └── Substituted (name: 'RES_0603_N', value: '47R 0603 1% 75V 100mW'), by (name_pattern: 'RES_0603.*', value_pattern: '47R 1% 75V'), comment: 'Add size code', comment: 'Use 100mW by default'
│       └── manufacturer: 'YAGEO', mpn: 'RC0603FR-0747RL' (Auto-selected)
├── R16 (name: 'RES_2512_N', value: '0R075 1206 1.5W 1%')
│   └── Substituted (name: 'RES_2512_N', value: '0R075 1206 3W 1%'), by (name_pattern: 'RES_2512.*', value_pattern: '0R075 1206 1.5W 1%'), de-rate: 'from 1.5W to 3W'
│       └── manufacturer: 'UNI-ROYAL(Uniroyal Elec)', mpn: 'LR123WF750MT4E' (Auto-selected)
├── R17 (name: 'RES_0603_N', value: '2R2')
│   └── Substituted (name: 'RES_0603_N', value: '2R2 0603 1% 75V 100mW'), by (name_pattern: 'RES_0603_N', value_pattern: '2R2'), comment: 'Use 1% by default', comment: 'Use 75V by default', comment: 'Use 100mW by default'
│       └── manufacturer: 'YAGEO', mpn: 'RC0603FR-072R2L' (Auto-selected)
├── R18 (name: 'RES_0603_N', value: '470R')
│   └── Substituted (name: 'RES_0603_N', value: '470R 0603 1% 75V 100mW'), by (name_pattern: 'RES_0603_N', value_pattern: '470R'), comment: 'Use 1% by default', comment: 'Use 75V by default', comment: 'Use 100mW by default'
│       └── manufacturer: 'YAGEO', mpn: 'RC0603FR-07470RL' (Auto-selected)
├── R19 (name: 'RES_0603_N', value: '680R')
│   └── Substituted (name: 'RES_0603_N', value: '680R 0603 1% 75V 100mW'), by (name_pattern: 'RES_0603_N', value_pattern: '680R'), comment: 'Use 1% by default', comment: 'Use 75V by default', comment: 'Use 100mW by default'
│       └── manufacturer: 'YAGEO', mpn: 'RC0603FR-07680RL' (Auto-selected)
├── R20 (name: 'RES_0603_N', value: '100K')
│   └── Substituted (name: 'RES_0603_N', value: '100K 0603 1% 75V 100mW'), by (name_pattern: 'RES_0603_N', value_pattern: '100K'), comment: 'Use 1% by default', comment: 'Use 75V by default', comment: '100mW by default'
│       └── manufacturer: 'YAGEO', mpn: 'RC0603FR-07100KL' (Auto-selected)
├── R21 (name: 'RES_0603_N', value: '10K')
│   └── Substituted (name: 'RES_0603_N', value: '10K 0603 1% 75V 100mW'), by (name_pattern: 'RES_0603_N', value_pattern: '10K'), comment: 'Use 1% by default', comment: 'Use 75V by default', comment: 'Use 100mW by default'
│       └── manufacturer: 'YAGEO', mpn: 'RC0603FR-0710KL' (Auto-selected)
├── R22 (name: 'RES_0603_N', value: '10K')
│   └── Substituted (name: 'RES_0603_N', value: '10K 0603 1% 75V 100mW'), by (name_pattern: 'RES_0603_N', value_pattern: '10K'), comment: 'Use 1% by default', comment: 'Use 75V by default', comment: 'Use 100mW by default'
│       └── manufacturer: 'YAGEO', mpn: 'RC0603FR-0710KL' (Auto-selected)
├── R23 (name: 'RES_0603_N', value: '10K')
│   └── Substituted (name: 'RES_0603_N', value: '10K 0603 1% 75V 100mW'), by (name_pattern: 'RES_0603_N', value_pattern: '10K'), comment: 'Use 1% by default', comment: 'Use 75V by default', comment: 'Use 100mW by default'
│       └── manufacturer: 'YAGEO', mpn: 'RC0603FR-0710KL' (Auto-selected)
├── R24 (name: 'RES_0603_N', value: '10K')
│   └── Substituted (name: 'RES_0603_N', value: '10K 0603 1% 75V 100mW'), by (name_pattern: 'RES_0603_N', value_pattern: '10K'), comment: 'Use 1% by default', comment: 'Use 75V by default', comment: 'Use 100mW by default'
│       └── manufacturer: 'YAGEO', mpn: 'RC0603FR-0710KL' (Auto-selected)
├── R25 (name: 'RES_0603_N', value: '0R')
│   └── Substituted (name: 'RES_0603_N', value: '0R 0603 333mW 75V'), by (name_pattern: 'RES_0603_N', value_pattern: '0R'), comment: 'Use 333mW by default', comment: 'Use 75V by default'
│       └── manufacturer: 'Vishay Intertech', mpn: 'CRCW06030000Z0EAHP' (Auto-selected)
├── R26 (name: 'RES_0603_N', value: '0R')
│   └── Substituted (name: 'RES_0603_N', value: '0R 0603 333mW 75V'), by (name_pattern: 'RES_0603_N', value_pattern: '0R'), comment: 'Use 333mW by default', comment: 'Use 75V by default'
│       └── manufacturer: 'Vishay Intertech', mpn: 'CRCW06030000Z0EAHP' (Auto-selected)
├── R27 (name: 'RES_0603_N', value: '100K')
│   └── Substituted (name: 'RES_0603_N', value: '100K 0603 1% 75V 100mW'), by (name_pattern: 'RES_0603_N', value_pattern: '100K'), comment: 'Use 1% by default', comment: 'Use 75V by default', comment: '100mW by default'
│       └── manufacturer: 'YAGEO', mpn: 'RC0603FR-07100KL' (Auto-selected)
├── R28 (name: 'RES_0603_N', value: '100K')
│   └── Substituted (name: 'RES_0603_N', value: '100K 0603 1% 75V 100mW'), by (name_pattern: 'RES_0603_N', value_pattern: '100K'), comment: 'Use 1% by default', comment: 'Use 75V by default', comment: '100mW by default'
│       └── manufacturer: 'YAGEO', mpn: 'RC0603FR-07100KL' (Auto-selected)
├── R29 (name: 'RES_0603_N', value: '100K')
│   └── Substituted (name: 'RES_0603_N', value: '100K 0603 1% 75V 100mW'), by (name_pattern: 'RES_0603_N', value_pattern: '100K'), comment: 'Use 1% by default', comment: 'Use 75V by default', comment: '100mW by default'
│       └── manufacturer: 'YAGEO', mpn: 'RC0603FR-07100KL' (Auto-selected)
├── R30 (name: 'RES_0603_N', value: '100K')
│   └── Substituted (name: 'RES_0603_N', value: '100K 0603 1% 75V 100mW'), by (name_pattern: 'RES_0603_N', value_pattern: '100K'), comment: 'Use 1% by default', comment: 'Use 75V by default', comment: '100mW by default'
│       └── manufacturer: 'YAGEO', mpn: 'RC0603FR-07100KL' (Auto-selected)
├── R31 (name: 'RES_0603_N', value: '100K')
│   └── Substituted (name: 'RES_0603_N', value: '100K 0603 1% 75V 100mW'), by (name_pattern: 'RES_0603_N', value_pattern: '100K'), comment: 'Use 1% by default', comment: 'Use 75V by default', comment: '100mW by default'
│       └── manufacturer: 'YAGEO', mpn: 'RC0603FR-07100KL' (Auto-selected)
├── R32 (name: 'RES_0603_N', value: '0R')
│   └── Substituted (name: 'RES_0603_N', value: '0R 0603 333mW 75V'), by (name_pattern: 'RES_0603_N', value_pattern: '0R'), comment: 'Use 333mW by default', comment: 'Use 75V by default'
│       └── manufacturer: 'Vishay Intertech', mpn: 'CRCW06030000Z0EAHP' (Auto-selected)
├── R33 (name: 'RES_0402', value: '309K 0402 1%')
│   └── Substituted (name: 'RES_0402', value: '309K 0402 1% 50V 62.5mW'), by (name_pattern: 'RES_0402', value_pattern: '309K 0402 1%'), comment: 'Use 50V by default', comment: 'Use 62.5mW by default'
│       └── manufacturer: 'YAGEO', mpn: 'RC0402FR-07309KL' (Auto-selected)
├── R34 (name: 'RES_0402', value: '22K1 0402 1%')
│   └── Substituted (name: 'RES_0402', value: '22K1 0402 1% 50V 62.5mW'), by (name_pattern: 'RES_0402', value_pattern: '22K1 0402 1%'), comment: 'Use 50V by default', comment: 'Use 62.5mW by default'
│       └── manufacturer: 'YAGEO', mpn: 'RC0402FR-0722K1L' (Auto-selected)
├── R35 (name: 'RES_0603_N', value: '22R 1% 75V')
│   └── Substituted (name: 'RES_0603_N', value: '22R 0603 1% 75V 100mW'), by (name_pattern: 'RES_0603.*', value_pattern: '22R 1% 75V'), comment: 'Add size code', comment: 'Use 100mW by default'
│       └── manufacturer: 'YAGEO', mpn: 'RC0603FR-0722RL' (Auto-selected)
├── R36 (name: 'RES_0603_N', value: '22R 1% 75V')
│   └── Substituted (name: 'RES_0603_N', value: '22R 0603 1% 75V 100mW'), by (name_pattern: 'RES_0603.*', value_pattern: '22R 1% 75V'), comment: 'Add size code', comment: 'Use 100mW by default'
│       └── manufacturer: 'YAGEO', mpn: 'RC0603FR-0722RL' (Auto-selected)
├── R37 (name: 'RES_0603_N', value: '22R 1% 75V')
│   └── Substituted (name: 'RES_0603_N', value: '22R 0603 1% 75V 100mW'), by (name_pattern: 'RES_0603.*', value_pattern: '22R 1% 75V'), comment: 'Add size code', comment: 'Use 100mW by default'
│       └── manufacturer: 'YAGEO', mpn: 'RC0603FR-0722RL' (Auto-selected)
├── R38 (name: 'RES_0603_N', value: '22R 1% 75V')
│   └── Substituted (name: 'RES_0603_N', value: '22R 0603 1% 75V 100mW'), by (name_pattern: 'RES_0603.*', value_pattern: '22R 1% 75V'), comment: 'Add size code', comment: 'Use 100mW by default'
│       └── manufacturer: 'YAGEO', mpn: 'RC0603FR-0722RL' (Auto-selected)
├── R39 (name: 'RES_0603_N', value: '47R 1% 75V')
│   └── Substituted (name: 'RES_0603_N', value: '47R 0603 1% 75V 100mW'), by (name_pattern: 'RES_0603.*', value_pattern: '47R 1% 75V'), comment: 'Add size code', comment: 'Use 100mW by default'
│       └── manufacturer: 'YAGEO', mpn: 'RC0603FR-0747RL' (Auto-selected)
├── R40 (name: 'RES_0603_N', value: '47R 1% 75V')
│   └── Substituted (name: 'RES_0603_N', value: '47R 0603 1% 75V 100mW'), by (name_pattern: 'RES_0603.*', value_pattern: '47R 1% 75V'), comment: 'Add size code', comment: 'Use 100mW by default'
│       └── manufacturer: 'YAGEO', mpn: 'RC0603FR-0747RL' (Auto-selected)
├── R41 (name: 'RES_2512_N', value: '0R075 1206 1.5W 1%')
│   └── Substituted (name: 'RES_2512_N', value: '0R075 1206 3W 1%'), by (name_pattern: 'RES_2512.*', value_pattern: '0R075 1206 1.5W 1%'), de-rate: 'from 1.5W to 3W'
│       └── manufacturer: 'UNI-ROYAL(Uniroyal Elec)', mpn: 'LR123WF750MT4E' (Auto-selected)
├── R42 (name: 'RES_0603_N', value: '22R 1% 75V')
│   └── Substituted (name: 'RES_0603_N', value: '22R 0603 1% 75V 100mW'), by (name_pattern: 'RES_0603.*', value_pattern: '22R 1% 75V'), comment: 'Add size code', comment: 'Use 100mW by default'
│       └── manufacturer: 'YAGEO', mpn: 'RC0603FR-0722RL' (Auto-selected)
├── R43 (name: 'RES_0603_N', value: '22R 1% 75V')
│   └── Substituted (name: 'RES_0603_N', value: '22R 0603 1% 75V 100mW'), by (name_pattern: 'RES_0603.*', value_pattern: '22R 1% 75V'), comment: 'Add size code', comment: 'Use 100mW by default'
│       └── manufacturer: 'YAGEO', mpn: 'RC0603FR-0722RL' (Auto-selected)
├── R44 (name: 'RES_0603_N', value: '22R 1% 75V')
│   └── Substituted (name: 'RES_0603_N', value: '22R 0603 1% 75V 100mW'), by (name_pattern: 'RES_0603.*', value_pattern: '22R 1% 75V'), comment: 'Add size code', comment: 'Use 100mW by default'
│       └── manufacturer: 'YAGEO', mpn: 'RC0603FR-0722RL' (Auto-selected)
├── R45 (name: 'RES_0603_N', value: '22R 1% 75V')
│   └── Substituted (name: 'RES_0603_N', value: '22R 0603 1% 75V 100mW'), by (name_pattern: 'RES_0603.*', value_pattern: '22R 1% 75V'), comment: 'Add size code', comment: 'Use 100mW by default'
│       └── manufacturer: 'YAGEO', mpn: 'RC0603FR-0722RL' (Auto-selected)
├── R46 (name: 'RES_0603_N', value: '47R 1% 75V')
│   └── Substituted (name: 'RES_0603_N', value: '47R 0603 1% 75V 100mW'), by (name_pattern: 'RES_0603.*', value_pattern: '47R 1% 75V'), comment: 'Add size code', comment: 'Use 100mW by default'
│       └── manufacturer: 'YAGEO', mpn: 'RC0603FR-0747RL' (Auto-selected)
├── R47 (name: 'RES_0603_N', value: '47R 1% 75V')
│   └── Substituted (name: 'RES_0603_N', value: '47R 0603 1% 75V 100mW'), by (name_pattern: 'RES_0603.*', value_pattern: '47R 1% 75V'), comment: 'Add size code', comment: 'Use 100mW by default'
│       └── manufacturer: 'YAGEO', mpn: 'RC0603FR-0747RL' (Auto-selected)
├── R48 (name: 'RES_2512_N', value: '0R075 1206 1.5W 1%')
│   └── Substituted (name: 'RES_2512_N', value: '0R075 1206 3W 1%'), by (name_pattern: 'RES_2512.*', value_pattern: '0R075 1206 1.5W 1%'), de-rate: 'from 1.5W to 3W'
│       └── manufacturer: 'UNI-ROYAL(Uniroyal Elec)', mpn: 'LR123WF750MT4E' (Auto-selected)
├── R49 (name: 'RES_0603_N', value: '2R2')
│   └── Substituted (name: 'RES_0603_N', value: '2R2 0603 1% 75V 100mW'), by (name_pattern: 'RES_0603_N', value_pattern: '2R2'), comment: 'Use 1% by default', comment: 'Use 75V by default', comment: 'Use 100mW by default'
│       └── manufacturer: 'YAGEO', mpn: 'RC0603FR-072R2L' (Auto-selected)
├── R50 (name: 'RES_0603_N', value: '0R')
│   └── Substituted (name: 'RES_0603_N', value: '0R 0603 333mW 75V'), by (name_pattern: 'RES_0603_N', value_pattern: '0R'), comment: 'Use 333mW by default', comment: 'Use 75V by default'
│       └── manufacturer: 'Vishay Intertech', mpn: 'CRCW06030000Z0EAHP' (Auto-selected)
├── R51 (name: 'RES_0603_N', value: '0R')
│   └── Substituted (name: 'RES_0603_N', value: '0R 0603 333mW 75V'), by (name_pattern: 'RES_0603_N', value_pattern: '0R'), comment: 'Use 333mW by default', comment: 'Use 75V by default'
│       └── manufacturer: 'Vishay Intertech', mpn: 'CRCW06030000Z0EAHP' (Auto-selected)
├── R52 (name: 'RES_0603_N', value: '10K')
│   └── Substituted (name: 'RES_0603_N', value: '10K 0603 1% 75V 100mW'), by (name_pattern: 'RES_0603_N', value_pattern: '10K'), comment: 'Use 1% by default', comment: 'Use 75V by default', comment: 'Use 100mW by default'
│       └── manufacturer: 'YAGEO', mpn: 'RC0603FR-0710KL' (Auto-selected)
├── R53 (name: 'RES_0603_N', value: '10K')
│   └── Substituted (name: 'RES_0603_N', value: '10K 0603 1% 75V 100mW'), by (name_pattern: 'RES_0603_N', value_pattern: '10K'), comment: 'Use 1% by default', comment: 'Use 75V by default', comment: 'Use 100mW by default'
│       └── manufacturer: 'YAGEO', mpn: 'RC0603FR-0710KL' (Auto-selected)
├── R54 (name: 'RES_0603_N', value: '2K2')
│   └── Substituted (name: 'RES_0603_N', value: '2K2 0603 1% 75V 100mW'), by (name_pattern: 'RES_0603_N', value_pattern: '2K2'), comment: 'Use 1% by default', comment: 'Use 75V by default', comment: 'Use 100mW by default'
│       └── manufacturer: 'YAGEO', mpn: 'RC0603FR-072K2L' (Auto-selected)
├── R55 (name: 'RES_0603_N', value: '10K')
│   └── Substituted (name: 'RES_0603_N', value: '10K 0603 1% 75V 100mW'), by (name_pattern: 'RES_0603_N', value_pattern: '10K'), comment: 'Use 1% by default', comment: 'Use 75V by default', comment: 'Use 100mW by default'
│       └── manufacturer: 'YAGEO', mpn: 'RC0603FR-0710KL' (Auto-selected)
├── R56 (name: 'RES_0603_N', value: '10K')
│   └── Substituted (name: 'RES_0603_N', value: '10K 0603 1% 75V 100mW'), by (name_pattern: 'RES_0603_N', value_pattern: '10K'), comment: 'Use 1% by default', comment: 'Use 75V by default', comment: 'Use 100mW by default'
│       └── manufacturer: 'YAGEO', mpn: 'RC0603FR-0710KL' (Auto-selected)
├── R57 (name: 'RES_2512_N', value: '0R075 1206 1.5W 1%')
│   └── Substituted (name: 'RES_2512_N', value: '0R075 1206 3W 1%'), by (name_pattern: 'RES_2512.*', value_pattern: '0R075 1206 1.5W 1%'), de-rate: 'from 1.5W to 3W'
│       └── manufacturer: 'UNI-ROYAL(Uniroyal Elec)', mpn: 'LR123WF750MT4E' (Auto-selected)
├── R58 (name: 'RES_2512_N', value: '0R075 1206 1.5W 1%')
│   └── Substituted (name: 'RES_2512_N', value: '0R075 1206 3W 1%'), by (name_pattern: 'RES_2512.*', value_pattern: '0R075 1206 1.5W 1%'), de-rate: 'from 1.5W to 3W'
│       └── manufacturer: 'UNI-ROYAL(Uniroyal Elec)', mpn: 'LR123WF750MT4E' (Auto-selected)
├── R59 (name: 'RES_2512_N', value: '0R075 1206 1.5W 1%')
│   └── Substituted (name: 'RES_2512_N', value: '0R075 1206 3W 1%'), by (name_pattern: 'RES_2512.*', value_pattern: '0R075 1206 1.5W 1%'), de-rate: 'from 1.5W to 3W'
│       └── manufacturer: 'UNI-ROYAL(Uniroyal Elec)', mpn: 'LR123WF750MT4E' (Auto-selected)
├── R60 (name: 'RES_2512_N', value: '0R075 1206 1.5W 1%')
│   └── Substituted (name: 'RES_2512_N', value: '0R075 1206 3W 1%'), by (name_pattern: 'RES_2512.*', value_pattern: '0R075 1206 1.5W 1%'), de-rate: 'from 1.5W to 3W'
│       └── manufacturer: 'UNI-ROYAL(Uniroyal Elec)', mpn: 'LR123WF750MT4E' (Auto-selected)
├── R65 (name: 'RES_2512_N', value: '3K 1206 1W')
│   └── Substituted (name: 'RES_2512_N', value: '3K 1206 1W 5%'), by (name_pattern: 'RES_2512.*', value_pattern: '3K 1206 1W'), comment: 'Use 5% by default'
│       └── manufacturer: 'YAGEO', mpn: 'RC2512JK-073K3L' (Auto-selected)
├── R155 (name: 'YC164-FR-072KL', value: '2K')
│   └── manufacturer: 'YAGEO', mpn: 'YC164-FR-072KL' (Auto-selected)
├── R156 (name: 'YC164-FR-072KL', value: '2K')
│   └── manufacturer: 'YAGEO', mpn: 'YC164-FR-072KL' (Auto-selected)
├── RV1 (name: 'RES_1206_N', value: '1210 54Vclamp')
│   └── Substituted (name: 'RES_1206_N', value: 'AV20K1210401NIR1'), by (name_pattern: 'RES_1206_N', value_pattern: '1210 54Vclamp'), comment: ''
│       └── manufacturer: 'BOURNS', mpn: 'AV20K1210401NIR1' (Auto-selected)
├── RV2 (name: 'RES_1206_N', value: '1210 54Vclamp')
│   └── Substituted (name: 'RES_1206_N', value: 'AV20K1210401NIR1'), by (name_pattern: 'RES_1206_N', value_pattern: '1210 54Vclamp'), comment: ''
│       └── manufacturer: 'BOURNS', mpn: 'AV20K1210401NIR1' (Auto-selected)
├── RV3 (name: 'RES_1206_N', value: '1210 54Vclamp')
│   └── Substituted (name: 'RES_1206_N', value: 'AV20K1210401NIR1'), by (name_pattern: 'RES_1206_N', value_pattern: '1210 54Vclamp'), comment: ''
│       └── manufacturer: 'BOURNS', mpn: 'AV20K1210401NIR1' (Auto-selected)
├── RV4 (name: 'RES_1206_N', value: '1210 54Vclamp')
│   └── Substituted (name: 'RES_1206_N', value: 'AV20K1210401NIR1'), by (name_pattern: 'RES_1206_N', value_pattern: '1210 54Vclamp'), comment: ''
│       └── manufacturer: 'BOURNS', mpn: 'AV20K1210401NIR1' (Auto-selected)
├── U1 (name: 'LMR51610YDBVR', value: '1100kHz PFM')
│   └── manufacturer: 'Texas Instruments', mpn: 'LMR51610YDBVR' (Auto-selected)
├── U2 (name: 'TMC5160A-TA-T', value: '')
│   └── manufacturer: 'TRINAMIC Motion Control GmbH', mpn: 'TMC5160A-TA-T' (Auto-selected)
├── U3 (name: 'LMR51610YDBVR', value: '1100kHz PFM')
│   └── manufacturer: 'Texas Instruments', mpn: 'LMR51610YDBVR' (Auto-selected)
├── U4 (name: 'ISO6762DWR', value: '')
│   └── manufacturer: 'Texas Instruments', mpn: 'ISO6762DWR' (Auto-selected)
├── U5 (name: 'ISO6762DWR', value: '')
│   └── manufacturer: 'Texas Instruments', mpn: 'ISO6762DWR' (Auto-selected)
├── U6 (name: 'TMC5160A-TA-T', value: '')
│   └── manufacturer: 'TRINAMIC Motion Control GmbH', mpn: 'TMC5160A-TA-T' (Auto-selected)
├── U7 (name: 'ISO6762DWR', value: '')
│   └── manufacturer: 'Texas Instruments', mpn: 'ISO6762DWR' (Auto-selected)
├── U42 (name: 'AM26C32IPWR', value: '')
│   └── manufacturer: 'Texas Instruments', mpn: 'AM26C32IPWR' (Auto-selected)
├── U43 (name: 'AM26C32IPWR', value: '')
│   └── manufacturer: 'Texas Instruments', mpn: 'AM26C32IPWR' (Auto-selected)
└── X2 (name: '01550900M', value: '')
    └── Substituted (name: 'XFCN', value: 'XF-154'), by (name_pattern: '01550900M', value_pattern: '.*'), comment: 'Use XFCN brand.'
        └── manufacturer: 'XFCN', mpn: 'XF-154' (Auto-selected)

variantbuilder_app: All placements mapped!
variantbuilder_app: Output written to 'MakerPnPControl-stepper1_variant1_placements.csv'
variantbuilder_app: BOM written to 'MakerPnPControl-stepper1_variant1_bom.csv'

Process finished with exit code 0

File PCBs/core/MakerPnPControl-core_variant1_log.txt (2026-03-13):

D:\Users\Hydra\Documents\dev\projects\makerpnp\makerpnp\target\release\variantbuilder_cli.exe @MakerPnPControl-core_variant1.args
stores::eda_placements: Loading eda placements. source: Export/MakerPnPControl-Core-PCB/MakerPnPControl-core-PnP.csv
variantbuilder_app: Loaded 205 placements
variantbuilder_app: excluding placements: ["J401"]
stores::substitutions: Loading eda substitutions. source: global-substitutions.csv
variantbuilder_app: Loaded 108 substitution rules from global-substitutions.csv
variantbuilder_app: disabling placements: []
stores::parts: Loading parts. source: parts.csv
variantbuilder_app: Loaded 165 parts
stores::part_mappings: Loading part mappings. source: part-mappings.csv
variantbuilder_app: Loaded 160 part mappings
variantbuilder_app: Loaded 0 load-out items
variantbuilder_app: Loaded 0 assembly rules
variantbuilder_app: Assembly variant: Default
variantbuilder_app: Ref_des list:
variantbuilder_app: Matched 204 placements for assembly variant
variantbuilder_app: Mapping Result
├── C1 (name: 'CAP_0402', value: '100nF 6.3V 0402')
│   └── Substituted (name: 'CAP_0402', value: '100nF 6.3V 0402 X7R 10%'), by (name_pattern: 'CAP_0402', value_pattern: '100nF 6.3V 0402'), comment: 'Use X7R 10% by default'
│       └── Substituted (name: 'CAP_0402', value: '100nF 16V 0402 X7R 10%'), by (name_pattern: 'CAP_0402', value_pattern: '100nF 6.3V 0402 X7R 10%'), de-rate: 'from 6.3V to 16V'
│           └── manufacturer: 'Samsung Electro-Mechanics', mpn: 'CL05B104KO5NNNC' (Auto-selected)
├── C2 (name: 'CAP_0603', value: '4.7uF 6.3V 0603 X5R 10%')
│   └── Substituted (name: 'CAP_0603', value: '4.7uF 16V 0603 X5R 10%'), by (name_pattern: 'CAP_0603', value_pattern: '4.7uF 6.3V 0603 X5R 10%'), de-rate: 'from 6.3V to 16V'
│       └── manufacturer: 'Samsung Electro-Mechanics', mpn: 'CL10A475KO8NNNC' (Auto-selected)
├── C3 (name: 'CAP_0402', value: '200pF 16V 0402 X5R')
│   └── Substituted (name: 'CAP_0402', value: '200pF 50V 0402 X5R 10%'), by (name_pattern: 'CAP_0402', value_pattern: '200pF 16V 0402 X5R'), de-rate: 'from 16V to 50V', comment: 'use 10% by default'
│       └── manufacturer: 'Murata Electronics', mpn: 'GRM155R71H221KA01D' (Auto-selected)
├── C4 (name: 'CAP_0805_N', value: '22uF 25V X5R')
│   └── Substituted (name: 'CAP_0805_N', value: '22uF 25V X5R 20%'), by (name_pattern: 'CAP_0805_N', value_pattern: '22uF 25V X5R.*'), comment: 'Use 20% by default'
│       └── manufacturer: 'Samsung Electro-Mechanics', mpn: 'CL21A226MAQNNNE' (Auto-selected)
├── C5 (name: 'CAP_0805_N', value: '22uF 25V X5R')
│   └── Substituted (name: 'CAP_0805_N', value: '22uF 25V X5R 20%'), by (name_pattern: 'CAP_0805_N', value_pattern: '22uF 25V X5R.*'), comment: 'Use 20% by default'
│       └── manufacturer: 'Samsung Electro-Mechanics', mpn: 'CL21A226MAQNNNE' (Auto-selected)
├── C6 (name: 'CAP_0603', value: '4.7uF 6.3V 0603 X5R 10%')
│   └── Substituted (name: 'CAP_0603', value: '4.7uF 16V 0603 X5R 10%'), by (name_pattern: 'CAP_0603', value_pattern: '4.7uF 6.3V 0603 X5R 10%'), de-rate: 'from 6.3V to 16V'
│       └── manufacturer: 'Samsung Electro-Mechanics', mpn: 'CL10A475KO8NNNC' (Auto-selected)
├── C7 (name: 'CAP_0402', value: '200pF 16V 0402 X5R')
│   └── Substituted (name: 'CAP_0402', value: '200pF 50V 0402 X5R 10%'), by (name_pattern: 'CAP_0402', value_pattern: '200pF 16V 0402 X5R'), de-rate: 'from 16V to 50V', comment: 'use 10% by default'
│       └── manufacturer: 'Murata Electronics', mpn: 'GRM155R71H221KA01D' (Auto-selected)
├── C8 (name: 'CAP_0805_N', value: '22uF 25V X5R')
│   └── Substituted (name: 'CAP_0805_N', value: '22uF 25V X5R 20%'), by (name_pattern: 'CAP_0805_N', value_pattern: '22uF 25V X5R.*'), comment: 'Use 20% by default'
│       └── manufacturer: 'Samsung Electro-Mechanics', mpn: 'CL21A226MAQNNNE' (Auto-selected)
├── C9 (name: 'CAP_0805_N', value: '22uF 25V X5R')
│   └── Substituted (name: 'CAP_0805_N', value: '22uF 25V X5R 20%'), by (name_pattern: 'CAP_0805_N', value_pattern: '22uF 25V X5R.*'), comment: 'Use 20% by default'
│       └── manufacturer: 'Samsung Electro-Mechanics', mpn: 'CL21A226MAQNNNE' (Auto-selected)
├── C10 (name: 'CAP_0603', value: '4.7uF 6.3V 0603 X5R 10%')
│   └── Substituted (name: 'CAP_0603', value: '4.7uF 16V 0603 X5R 10%'), by (name_pattern: 'CAP_0603', value_pattern: '4.7uF 6.3V 0603 X5R 10%'), de-rate: 'from 6.3V to 16V'
│       └── manufacturer: 'Samsung Electro-Mechanics', mpn: 'CL10A475KO8NNNC' (Auto-selected)
├── C11 (name: 'CAP_0402', value: '200pF 16V 0402 X5R')
│   └── Substituted (name: 'CAP_0402', value: '200pF 50V 0402 X5R 10%'), by (name_pattern: 'CAP_0402', value_pattern: '200pF 16V 0402 X5R'), de-rate: 'from 16V to 50V', comment: 'use 10% by default'
│       └── manufacturer: 'Murata Electronics', mpn: 'GRM155R71H221KA01D' (Auto-selected)
├── C12 (name: 'CAP_0805_N', value: '22uF 25V X5R')
│   └── Substituted (name: 'CAP_0805_N', value: '22uF 25V X5R 20%'), by (name_pattern: 'CAP_0805_N', value_pattern: '22uF 25V X5R.*'), comment: 'Use 20% by default'
│       └── manufacturer: 'Samsung Electro-Mechanics', mpn: 'CL21A226MAQNNNE' (Auto-selected)
├── C13 (name: 'CAP_0805_N', value: '22uF 25V X5R')
│   └── Substituted (name: 'CAP_0805_N', value: '22uF 25V X5R 20%'), by (name_pattern: 'CAP_0805_N', value_pattern: '22uF 25V X5R.*'), comment: 'Use 20% by default'
│       └── manufacturer: 'Samsung Electro-Mechanics', mpn: 'CL21A226MAQNNNE' (Auto-selected)
├── C101 (name: 'CAP_0402', value: '4.7uF 6.3V 0402 10%')
│   └── Substituted (name: 'CAP_0402', value: '4.7uF 6.3V 0402 X5R 10%'), by (name_pattern: 'CAP_0402', value_pattern: '4.7uF 6.3V 0402 10%'), comment: 'Use X5R by default'
│       └── Substituted (name: 'CAP_0402', value: '4.7uF 10V 0402 X5R 10%'), by (name_pattern: 'CAP_0402', value_pattern: '4.7uF 6.3V 0402 X5R 10%'), de-rate: 'from 6.3V to 10V'
│           └── manufacturer: 'Murata Electronics', mpn: 'GRM155R61A475KEAAD' (Auto-selected)
├── C102 (name: 'CAP_0603', value: '10uF 6.3V 0603 X5R 10%')
│   └── Substituted (name: 'CAP_0603', value: '10uF 25V 0603 X5R 10%'), by (name_pattern: 'CAP_0603', value_pattern: '10uF 6.3V 0603 X5R 10%'), de-rate: 'from 6.3V to 25V'
│       └── manufacturer: 'Samsung Electro-Mechanics', mpn: 'CL10A106MA8NRNC' (Auto-selected)
├── C103 (name: 'CAP_0603', value: '10uF 6.3V 0603 X5R 10%')
│   └── Substituted (name: 'CAP_0603', value: '10uF 25V 0603 X5R 10%'), by (name_pattern: 'CAP_0603', value_pattern: '10uF 6.3V 0603 X5R 10%'), de-rate: 'from 6.3V to 25V'
│       └── manufacturer: 'Samsung Electro-Mechanics', mpn: 'CL10A106MA8NRNC' (Auto-selected)
├── C104 (name: 'CAP_0402', value: '100nF 6.3V 0402')
│   └── Substituted (name: 'CAP_0402', value: '100nF 6.3V 0402 X7R 10%'), by (name_pattern: 'CAP_0402', value_pattern: '100nF 6.3V 0402'), comment: 'Use X7R 10% by default'
│       └── Substituted (name: 'CAP_0402', value: '100nF 16V 0402 X7R 10%'), by (name_pattern: 'CAP_0402', value_pattern: '100nF 6.3V 0402 X7R 10%'), de-rate: 'from 6.3V to 16V'
│           └── manufacturer: 'Samsung Electro-Mechanics', mpn: 'CL05B104KO5NNNC' (Auto-selected)
├── C105 (name: 'CAP_0402', value: '100nF 6.3V 0402')
│   └── Substituted (name: 'CAP_0402', value: '100nF 6.3V 0402 X7R 10%'), by (name_pattern: 'CAP_0402', value_pattern: '100nF 6.3V 0402'), comment: 'Use X7R 10% by default'
│       └── Substituted (name: 'CAP_0402', value: '100nF 16V 0402 X7R 10%'), by (name_pattern: 'CAP_0402', value_pattern: '100nF 6.3V 0402 X7R 10%'), de-rate: 'from 6.3V to 16V'
│           └── manufacturer: 'Samsung Electro-Mechanics', mpn: 'CL05B104KO5NNNC' (Auto-selected)
├── C106 (name: 'CAP_0402', value: '100nF 6.3V 0402')
│   └── Substituted (name: 'CAP_0402', value: '100nF 6.3V 0402 X7R 10%'), by (name_pattern: 'CAP_0402', value_pattern: '100nF 6.3V 0402'), comment: 'Use X7R 10% by default'
│       └── Substituted (name: 'CAP_0402', value: '100nF 16V 0402 X7R 10%'), by (name_pattern: 'CAP_0402', value_pattern: '100nF 6.3V 0402 X7R 10%'), de-rate: 'from 6.3V to 16V'
│           └── manufacturer: 'Samsung Electro-Mechanics', mpn: 'CL05B104KO5NNNC' (Auto-selected)
├── C107 (name: 'CAP_0402', value: '100nF 6.3V 0402')
│   └── Substituted (name: 'CAP_0402', value: '100nF 6.3V 0402 X7R 10%'), by (name_pattern: 'CAP_0402', value_pattern: '100nF 6.3V 0402'), comment: 'Use X7R 10% by default'
│       └── Substituted (name: 'CAP_0402', value: '100nF 16V 0402 X7R 10%'), by (name_pattern: 'CAP_0402', value_pattern: '100nF 6.3V 0402 X7R 10%'), de-rate: 'from 6.3V to 16V'
│           └── manufacturer: 'Samsung Electro-Mechanics', mpn: 'CL05B104KO5NNNC' (Auto-selected)
├── C108 (name: 'CAP_0402', value: '100nF 6.3V 0402')
│   └── Substituted (name: 'CAP_0402', value: '100nF 6.3V 0402 X7R 10%'), by (name_pattern: 'CAP_0402', value_pattern: '100nF 6.3V 0402'), comment: 'Use X7R 10% by default'
│       └── Substituted (name: 'CAP_0402', value: '100nF 16V 0402 X7R 10%'), by (name_pattern: 'CAP_0402', value_pattern: '100nF 6.3V 0402 X7R 10%'), de-rate: 'from 6.3V to 16V'
│           └── manufacturer: 'Samsung Electro-Mechanics', mpn: 'CL05B104KO5NNNC' (Auto-selected)
├── C109 (name: 'CAP_0402', value: '100nF 6.3V 0402')
│   └── Substituted (name: 'CAP_0402', value: '100nF 6.3V 0402 X7R 10%'), by (name_pattern: 'CAP_0402', value_pattern: '100nF 6.3V 0402'), comment: 'Use X7R 10% by default'
│       └── Substituted (name: 'CAP_0402', value: '100nF 16V 0402 X7R 10%'), by (name_pattern: 'CAP_0402', value_pattern: '100nF 6.3V 0402 X7R 10%'), de-rate: 'from 6.3V to 16V'
│           └── manufacturer: 'Samsung Electro-Mechanics', mpn: 'CL05B104KO5NNNC' (Auto-selected)
├── C110 (name: 'CAP_0402', value: '100nF 6.3V 0402')
│   └── Substituted (name: 'CAP_0402', value: '100nF 6.3V 0402 X7R 10%'), by (name_pattern: 'CAP_0402', value_pattern: '100nF 6.3V 0402'), comment: 'Use X7R 10% by default'
│       └── Substituted (name: 'CAP_0402', value: '100nF 16V 0402 X7R 10%'), by (name_pattern: 'CAP_0402', value_pattern: '100nF 6.3V 0402 X7R 10%'), de-rate: 'from 6.3V to 16V'
│           └── manufacturer: 'Samsung Electro-Mechanics', mpn: 'CL05B104KO5NNNC' (Auto-selected)
├── C111 (name: 'CAP_0603', value: '10uF 6.3V 0603 X5R 10%')
│   └── Substituted (name: 'CAP_0603', value: '10uF 25V 0603 X5R 10%'), by (name_pattern: 'CAP_0603', value_pattern: '10uF 6.3V 0603 X5R 10%'), de-rate: 'from 6.3V to 25V'
│       └── manufacturer: 'Samsung Electro-Mechanics', mpn: 'CL10A106MA8NRNC' (Auto-selected)
├── C112 (name: 'CAP_0402', value: '100nF 6.3V 0402')
│   └── Substituted (name: 'CAP_0402', value: '100nF 6.3V 0402 X7R 10%'), by (name_pattern: 'CAP_0402', value_pattern: '100nF 6.3V 0402'), comment: 'Use X7R 10% by default'
│       └── Substituted (name: 'CAP_0402', value: '100nF 16V 0402 X7R 10%'), by (name_pattern: 'CAP_0402', value_pattern: '100nF 6.3V 0402 X7R 10%'), de-rate: 'from 6.3V to 16V'
│           └── manufacturer: 'Samsung Electro-Mechanics', mpn: 'CL05B104KO5NNNC' (Auto-selected)
├── C113 (name: 'CAP_0603', value: '4.7uF 6.3V 0603 X5R 10%')
│   └── Substituted (name: 'CAP_0603', value: '4.7uF 16V 0603 X5R 10%'), by (name_pattern: 'CAP_0603', value_pattern: '4.7uF 6.3V 0603 X5R 10%'), de-rate: 'from 6.3V to 16V'
│       └── manufacturer: 'Samsung Electro-Mechanics', mpn: 'CL10A475KO8NNNC' (Auto-selected)
├── C114 (name: 'CAP_0402', value: '100nF 6.3V 0402')
│   └── Substituted (name: 'CAP_0402', value: '100nF 6.3V 0402 X7R 10%'), by (name_pattern: 'CAP_0402', value_pattern: '100nF 6.3V 0402'), comment: 'Use X7R 10% by default'
│       └── Substituted (name: 'CAP_0402', value: '100nF 16V 0402 X7R 10%'), by (name_pattern: 'CAP_0402', value_pattern: '100nF 6.3V 0402 X7R 10%'), de-rate: 'from 6.3V to 16V'
│           └── manufacturer: 'Samsung Electro-Mechanics', mpn: 'CL05B104KO5NNNC' (Auto-selected)
├── C115 (name: 'CAP_0402', value: '100nF 6.3V 0402')
│   └── Substituted (name: 'CAP_0402', value: '100nF 6.3V 0402 X7R 10%'), by (name_pattern: 'CAP_0402', value_pattern: '100nF 6.3V 0402'), comment: 'Use X7R 10% by default'
│       └── Substituted (name: 'CAP_0402', value: '100nF 16V 0402 X7R 10%'), by (name_pattern: 'CAP_0402', value_pattern: '100nF 6.3V 0402 X7R 10%'), de-rate: 'from 6.3V to 16V'
│           └── manufacturer: 'Samsung Electro-Mechanics', mpn: 'CL05B104KO5NNNC' (Auto-selected)
├── C116 (name: 'CAP_0402', value: '200pF 16V 0402 X5R')
│   └── Substituted (name: 'CAP_0402', value: '200pF 50V 0402 X5R 10%'), by (name_pattern: 'CAP_0402', value_pattern: '200pF 16V 0402 X5R'), de-rate: 'from 16V to 50V', comment: 'use 10% by default'
│       └── manufacturer: 'Murata Electronics', mpn: 'GRM155R71H221KA01D' (Auto-selected)
├── C117 (name: 'CAP_0402', value: '100nF 6.3V 0402')
│   └── Substituted (name: 'CAP_0402', value: '100nF 6.3V 0402 X7R 10%'), by (name_pattern: 'CAP_0402', value_pattern: '100nF 6.3V 0402'), comment: 'Use X7R 10% by default'
│       └── Substituted (name: 'CAP_0402', value: '100nF 16V 0402 X7R 10%'), by (name_pattern: 'CAP_0402', value_pattern: '100nF 6.3V 0402 X7R 10%'), de-rate: 'from 6.3V to 16V'
│           └── manufacturer: 'Samsung Electro-Mechanics', mpn: 'CL05B104KO5NNNC' (Auto-selected)
├── C118 (name: 'CAP_0603', value: '10uF 6.3V 0603 X5R 20mOhm ESR 10%')
│   └── Substituted (name: 'CAP_0603', value: '10uF 25V 0603 X5R 10%'), by (name_pattern: 'CAP_0603', value_pattern: '10uF 6.3V 0603 X5R 20mOhm ESR 10%'), comment: 'H7 PSU Caps - Ignore ESR requirements', de-rate: 'to 25V'
│       └── manufacturer: 'Samsung Electro-Mechanics', mpn: 'CL10A106MA8NRNC' (Auto-selected)
├── C119 (name: 'CAP_0402', value: '100nF 6.3V 0402')
│   └── Substituted (name: 'CAP_0402', value: '100nF 6.3V 0402 X7R 10%'), by (name_pattern: 'CAP_0402', value_pattern: '100nF 6.3V 0402'), comment: 'Use X7R 10% by default'
│       └── Substituted (name: 'CAP_0402', value: '100nF 16V 0402 X7R 10%'), by (name_pattern: 'CAP_0402', value_pattern: '100nF 6.3V 0402 X7R 10%'), de-rate: 'from 6.3V to 16V'
│           └── manufacturer: 'Samsung Electro-Mechanics', mpn: 'CL05B104KO5NNNC' (Auto-selected)
├── C120 (name: 'CAP_0603', value: '10uF 6.3V 0603 X5R 20mOhm ESR 10%')
│   └── Substituted (name: 'CAP_0603', value: '10uF 25V 0603 X5R 10%'), by (name_pattern: 'CAP_0603', value_pattern: '10uF 6.3V 0603 X5R 20mOhm ESR 10%'), comment: 'H7 PSU Caps - Ignore ESR requirements', de-rate: 'to 25V'
│       └── manufacturer: 'Samsung Electro-Mechanics', mpn: 'CL10A106MA8NRNC' (Auto-selected)
├── C121 (name: 'CAP_0402', value: '2.2uF 6.3V 0402')
│   └── Substituted (name: 'CAP_0402', value: '2.2uF 6.3V 0402 X5R 10%'), by (name_pattern: 'CAP_0402', value_pattern: '2.2uF 6.3V 0402'), comment: 'Use X5R 10% by default'
│       └── manufacturer: 'Samsung Electro-Mechanics', mpn: 'CL05A225KP5NSNC' (Auto-selected)
├── C122 (name: 'CAP_0402', value: '2.2uF 6.3V 0402')
│   └── Substituted (name: 'CAP_0402', value: '2.2uF 6.3V 0402 X5R 10%'), by (name_pattern: 'CAP_0402', value_pattern: '2.2uF 6.3V 0402'), comment: 'Use X5R 10% by default'
│       └── manufacturer: 'Samsung Electro-Mechanics', mpn: 'CL05A225KP5NSNC' (Auto-selected)
├── C123 (name: 'CAP_0402', value: '1uF 6.3V 0402')
│   └── Substituted (name: 'CAP_0402', value: '1uF 6.3V 0402 X5R 10%'), by (name_pattern: 'CAP_0402', value_pattern: '1uF 6.3V 0402'), comment: 'Use X5R 10% by default'
│       └── Substituted (name: 'CAP_0402', value: '1uF 25V 0402 X5R 10%'), by (name_pattern: 'CAP_0402', value_pattern: '1uF 6.3V 0402 X5R 10%'), comment: ''
│           └── manufacturer: 'Samsung Electro-Mechanics', mpn: 'CL05A105KA5NQNC' (Auto-selected)
├── C124 (name: 'CAP_0402', value: '2.2uF 6.3V 0402')
│   └── Substituted (name: 'CAP_0402', value: '2.2uF 6.3V 0402 X5R 10%'), by (name_pattern: 'CAP_0402', value_pattern: '2.2uF 6.3V 0402'), comment: 'Use X5R 10% by default'
│       └── manufacturer: 'Samsung Electro-Mechanics', mpn: 'CL05A225KP5NSNC' (Auto-selected)
├── C125 (name: 'CAP_0402', value: '100nF 6.3V 0402')
│   └── Substituted (name: 'CAP_0402', value: '100nF 6.3V 0402 X7R 10%'), by (name_pattern: 'CAP_0402', value_pattern: '100nF 6.3V 0402'), comment: 'Use X7R 10% by default'
│       └── Substituted (name: 'CAP_0402', value: '100nF 16V 0402 X7R 10%'), by (name_pattern: 'CAP_0402', value_pattern: '100nF 6.3V 0402 X7R 10%'), de-rate: 'from 6.3V to 16V'
│           └── manufacturer: 'Samsung Electro-Mechanics', mpn: 'CL05B104KO5NNNC' (Auto-selected)
├── C126 (name: 'CAP_0402', value: '4.7uF 6.3V 0402 10%')
│   └── Substituted (name: 'CAP_0402', value: '4.7uF 6.3V 0402 X5R 10%'), by (name_pattern: 'CAP_0402', value_pattern: '4.7uF 6.3V 0402 10%'), comment: 'Use X5R by default'
│       └── Substituted (name: 'CAP_0402', value: '4.7uF 10V 0402 X5R 10%'), by (name_pattern: 'CAP_0402', value_pattern: '4.7uF 6.3V 0402 X5R 10%'), de-rate: 'from 6.3V to 10V'
│           └── manufacturer: 'Murata Electronics', mpn: 'GRM155R61A475KEAAD' (Auto-selected)
├── C127 (name: 'CAP_0402', value: '4.7uF 6.3V 0402 10%')
│   └── Substituted (name: 'CAP_0402', value: '4.7uF 6.3V 0402 X5R 10%'), by (name_pattern: 'CAP_0402', value_pattern: '4.7uF 6.3V 0402 10%'), comment: 'Use X5R by default'
│       └── Substituted (name: 'CAP_0402', value: '4.7uF 10V 0402 X5R 10%'), by (name_pattern: 'CAP_0402', value_pattern: '4.7uF 6.3V 0402 X5R 10%'), de-rate: 'from 6.3V to 10V'
│           └── manufacturer: 'Murata Electronics', mpn: 'GRM155R61A475KEAAD' (Auto-selected)
├── C128 (name: 'CAP_0402', value: '100nF 6.3V 0402')
│   └── Substituted (name: 'CAP_0402', value: '100nF 6.3V 0402 X7R 10%'), by (name_pattern: 'CAP_0402', value_pattern: '100nF 6.3V 0402'), comment: 'Use X7R 10% by default'
│       └── Substituted (name: 'CAP_0402', value: '100nF 16V 0402 X7R 10%'), by (name_pattern: 'CAP_0402', value_pattern: '100nF 6.3V 0402 X7R 10%'), de-rate: 'from 6.3V to 16V'
│           └── manufacturer: 'Samsung Electro-Mechanics', mpn: 'CL05B104KO5NNNC' (Auto-selected)
├── C129 (name: 'CAP_0402', value: '100nF 6.3V 0402')
│   └── Substituted (name: 'CAP_0402', value: '100nF 6.3V 0402 X7R 10%'), by (name_pattern: 'CAP_0402', value_pattern: '100nF 6.3V 0402'), comment: 'Use X7R 10% by default'
│       └── Substituted (name: 'CAP_0402', value: '100nF 16V 0402 X7R 10%'), by (name_pattern: 'CAP_0402', value_pattern: '100nF 6.3V 0402 X7R 10%'), de-rate: 'from 6.3V to 16V'
│           └── manufacturer: 'Samsung Electro-Mechanics', mpn: 'CL05B104KO5NNNC' (Auto-selected)
├── C130 (name: 'CAP_0402', value: '4.7uF 6.3V 0402 10%')
│   └── Substituted (name: 'CAP_0402', value: '4.7uF 6.3V 0402 X5R 10%'), by (name_pattern: 'CAP_0402', value_pattern: '4.7uF 6.3V 0402 10%'), comment: 'Use X5R by default'
│       └── Substituted (name: 'CAP_0402', value: '4.7uF 10V 0402 X5R 10%'), by (name_pattern: 'CAP_0402', value_pattern: '4.7uF 6.3V 0402 X5R 10%'), de-rate: 'from 6.3V to 10V'
│           └── manufacturer: 'Murata Electronics', mpn: 'GRM155R61A475KEAAD' (Auto-selected)
├── C131 (name: 'CAP_0402', value: '100nF 6.3V 0402')
│   └── Substituted (name: 'CAP_0402', value: '100nF 6.3V 0402 X7R 10%'), by (name_pattern: 'CAP_0402', value_pattern: '100nF 6.3V 0402'), comment: 'Use X7R 10% by default'
│       └── Substituted (name: 'CAP_0402', value: '100nF 16V 0402 X7R 10%'), by (name_pattern: 'CAP_0402', value_pattern: '100nF 6.3V 0402 X7R 10%'), de-rate: 'from 6.3V to 16V'
│           └── manufacturer: 'Samsung Electro-Mechanics', mpn: 'CL05B104KO5NNNC' (Auto-selected)
├── C132 (name: 'CAP_0805_N', value: '22uF 25V X5R')
│   └── Substituted (name: 'CAP_0805_N', value: '22uF 25V X5R 20%'), by (name_pattern: 'CAP_0805_N', value_pattern: '22uF 25V X5R.*'), comment: 'Use 20% by default'
│       └── manufacturer: 'Samsung Electro-Mechanics', mpn: 'CL21A226MAQNNNE' (Auto-selected)
├── C133 (name: 'CAP_0402', value: '100nF 6.3V 0402')
│   └── Substituted (name: 'CAP_0402', value: '100nF 6.3V 0402 X7R 10%'), by (name_pattern: 'CAP_0402', value_pattern: '100nF 6.3V 0402'), comment: 'Use X7R 10% by default'
│       └── Substituted (name: 'CAP_0402', value: '100nF 16V 0402 X7R 10%'), by (name_pattern: 'CAP_0402', value_pattern: '100nF 6.3V 0402 X7R 10%'), de-rate: 'from 6.3V to 16V'
│           └── manufacturer: 'Samsung Electro-Mechanics', mpn: 'CL05B104KO5NNNC' (Auto-selected)
├── C134 (name: 'CAP_0402', value: '100nF 6.3V 0402')
│   └── Substituted (name: 'CAP_0402', value: '100nF 6.3V 0402 X7R 10%'), by (name_pattern: 'CAP_0402', value_pattern: '100nF 6.3V 0402'), comment: 'Use X7R 10% by default'
│       └── Substituted (name: 'CAP_0402', value: '100nF 16V 0402 X7R 10%'), by (name_pattern: 'CAP_0402', value_pattern: '100nF 6.3V 0402 X7R 10%'), de-rate: 'from 6.3V to 16V'
│           └── manufacturer: 'Samsung Electro-Mechanics', mpn: 'CL05B104KO5NNNC' (Auto-selected)
├── C135 (name: 'CAP_0402', value: '4.7uF 6.3V 0402 10%')
│   └── Substituted (name: 'CAP_0402', value: '4.7uF 6.3V 0402 X5R 10%'), by (name_pattern: 'CAP_0402', value_pattern: '4.7uF 6.3V 0402 10%'), comment: 'Use X5R by default'
│       └── Substituted (name: 'CAP_0402', value: '4.7uF 10V 0402 X5R 10%'), by (name_pattern: 'CAP_0402', value_pattern: '4.7uF 6.3V 0402 X5R 10%'), de-rate: 'from 6.3V to 10V'
│           └── manufacturer: 'Murata Electronics', mpn: 'GRM155R61A475KEAAD' (Auto-selected)
├── C136 (name: 'CAP_0402', value: '100nF 6.3V 0402')
│   └── Substituted (name: 'CAP_0402', value: '100nF 6.3V 0402 X7R 10%'), by (name_pattern: 'CAP_0402', value_pattern: '100nF 6.3V 0402'), comment: 'Use X7R 10% by default'
│       └── Substituted (name: 'CAP_0402', value: '100nF 16V 0402 X7R 10%'), by (name_pattern: 'CAP_0402', value_pattern: '100nF 6.3V 0402 X7R 10%'), de-rate: 'from 6.3V to 16V'
│           └── manufacturer: 'Samsung Electro-Mechanics', mpn: 'CL05B104KO5NNNC' (Auto-selected)
├── C137 (name: 'CAP_0402', value: '100nF 6.3V 0402')
│   └── Substituted (name: 'CAP_0402', value: '100nF 6.3V 0402 X7R 10%'), by (name_pattern: 'CAP_0402', value_pattern: '100nF 6.3V 0402'), comment: 'Use X7R 10% by default'
│       └── Substituted (name: 'CAP_0402', value: '100nF 16V 0402 X7R 10%'), by (name_pattern: 'CAP_0402', value_pattern: '100nF 6.3V 0402 X7R 10%'), de-rate: 'from 6.3V to 16V'
│           └── manufacturer: 'Samsung Electro-Mechanics', mpn: 'CL05B104KO5NNNC' (Auto-selected)
├── C138 (name: 'CAP_0402', value: '100nF 6.3V 0402')
│   └── Substituted (name: 'CAP_0402', value: '100nF 6.3V 0402 X7R 10%'), by (name_pattern: 'CAP_0402', value_pattern: '100nF 6.3V 0402'), comment: 'Use X7R 10% by default'
│       └── Substituted (name: 'CAP_0402', value: '100nF 16V 0402 X7R 10%'), by (name_pattern: 'CAP_0402', value_pattern: '100nF 6.3V 0402 X7R 10%'), de-rate: 'from 6.3V to 16V'
│           └── manufacturer: 'Samsung Electro-Mechanics', mpn: 'CL05B104KO5NNNC' (Auto-selected)
├── C139 (name: 'CAP_0402', value: '100nF 6.3V 0402')
│   └── Substituted (name: 'CAP_0402', value: '100nF 6.3V 0402 X7R 10%'), by (name_pattern: 'CAP_0402', value_pattern: '100nF 6.3V 0402'), comment: 'Use X7R 10% by default'
│       └── Substituted (name: 'CAP_0402', value: '100nF 16V 0402 X7R 10%'), by (name_pattern: 'CAP_0402', value_pattern: '100nF 6.3V 0402 X7R 10%'), de-rate: 'from 6.3V to 16V'
│           └── manufacturer: 'Samsung Electro-Mechanics', mpn: 'CL05B104KO5NNNC' (Auto-selected)
├── C140 (name: 'CAP_0402', value: '100nF 6.3V 0402')
│   └── Substituted (name: 'CAP_0402', value: '100nF 6.3V 0402 X7R 10%'), by (name_pattern: 'CAP_0402', value_pattern: '100nF 6.3V 0402'), comment: 'Use X7R 10% by default'
│       └── Substituted (name: 'CAP_0402', value: '100nF 16V 0402 X7R 10%'), by (name_pattern: 'CAP_0402', value_pattern: '100nF 6.3V 0402 X7R 10%'), de-rate: 'from 6.3V to 16V'
│           └── manufacturer: 'Samsung Electro-Mechanics', mpn: 'CL05B104KO5NNNC' (Auto-selected)
├── C141 (name: 'CAP_0402', value: '100nF 6.3V 0402')
│   └── Substituted (name: 'CAP_0402', value: '100nF 6.3V 0402 X7R 10%'), by (name_pattern: 'CAP_0402', value_pattern: '100nF 6.3V 0402'), comment: 'Use X7R 10% by default'
│       └── Substituted (name: 'CAP_0402', value: '100nF 16V 0402 X7R 10%'), by (name_pattern: 'CAP_0402', value_pattern: '100nF 6.3V 0402 X7R 10%'), de-rate: 'from 6.3V to 16V'
│           └── manufacturer: 'Samsung Electro-Mechanics', mpn: 'CL05B104KO5NNNC' (Auto-selected)
├── C142 (name: 'CAP_0402', value: '100nF 6.3V 0402')
│   └── Substituted (name: 'CAP_0402', value: '100nF 6.3V 0402 X7R 10%'), by (name_pattern: 'CAP_0402', value_pattern: '100nF 6.3V 0402'), comment: 'Use X7R 10% by default'
│       └── Substituted (name: 'CAP_0402', value: '100nF 16V 0402 X7R 10%'), by (name_pattern: 'CAP_0402', value_pattern: '100nF 6.3V 0402 X7R 10%'), de-rate: 'from 6.3V to 16V'
│           └── manufacturer: 'Samsung Electro-Mechanics', mpn: 'CL05B104KO5NNNC' (Auto-selected)
├── C143 (name: 'CAP_0402', value: '100nF 6.3V 0402')
│   └── Substituted (name: 'CAP_0402', value: '100nF 6.3V 0402 X7R 10%'), by (name_pattern: 'CAP_0402', value_pattern: '100nF 6.3V 0402'), comment: 'Use X7R 10% by default'
│       └── Substituted (name: 'CAP_0402', value: '100nF 16V 0402 X7R 10%'), by (name_pattern: 'CAP_0402', value_pattern: '100nF 6.3V 0402 X7R 10%'), de-rate: 'from 6.3V to 16V'
│           └── manufacturer: 'Samsung Electro-Mechanics', mpn: 'CL05B104KO5NNNC' (Auto-selected)
├── C144 (name: 'CAP_0402', value: '100nF 6.3V 0402')
│   └── Substituted (name: 'CAP_0402', value: '100nF 6.3V 0402 X7R 10%'), by (name_pattern: 'CAP_0402', value_pattern: '100nF 6.3V 0402'), comment: 'Use X7R 10% by default'
│       └── Substituted (name: 'CAP_0402', value: '100nF 16V 0402 X7R 10%'), by (name_pattern: 'CAP_0402', value_pattern: '100nF 6.3V 0402 X7R 10%'), de-rate: 'from 6.3V to 16V'
│           └── manufacturer: 'Samsung Electro-Mechanics', mpn: 'CL05B104KO5NNNC' (Auto-selected)
├── C145 (name: 'CAP_0402', value: '100nF 6.3V 0402')
│   └── Substituted (name: 'CAP_0402', value: '100nF 6.3V 0402 X7R 10%'), by (name_pattern: 'CAP_0402', value_pattern: '100nF 6.3V 0402'), comment: 'Use X7R 10% by default'
│       └── Substituted (name: 'CAP_0402', value: '100nF 16V 0402 X7R 10%'), by (name_pattern: 'CAP_0402', value_pattern: '100nF 6.3V 0402 X7R 10%'), de-rate: 'from 6.3V to 16V'
│           └── manufacturer: 'Samsung Electro-Mechanics', mpn: 'CL05B104KO5NNNC' (Auto-selected)
├── C146 (name: 'CAP_0402', value: '100nF 6.3V 0402')
│   └── Substituted (name: 'CAP_0402', value: '100nF 6.3V 0402 X7R 10%'), by (name_pattern: 'CAP_0402', value_pattern: '100nF 6.3V 0402'), comment: 'Use X7R 10% by default'
│       └── Substituted (name: 'CAP_0402', value: '100nF 16V 0402 X7R 10%'), by (name_pattern: 'CAP_0402', value_pattern: '100nF 6.3V 0402 X7R 10%'), de-rate: 'from 6.3V to 16V'
│           └── manufacturer: 'Samsung Electro-Mechanics', mpn: 'CL05B104KO5NNNC' (Auto-selected)
├── C147 (name: 'CAP_0402', value: '100nF 6.3V 0402')
│   └── Substituted (name: 'CAP_0402', value: '100nF 6.3V 0402 X7R 10%'), by (name_pattern: 'CAP_0402', value_pattern: '100nF 6.3V 0402'), comment: 'Use X7R 10% by default'
│       └── Substituted (name: 'CAP_0402', value: '100nF 16V 0402 X7R 10%'), by (name_pattern: 'CAP_0402', value_pattern: '100nF 6.3V 0402 X7R 10%'), de-rate: 'from 6.3V to 16V'
│           └── manufacturer: 'Samsung Electro-Mechanics', mpn: 'CL05B104KO5NNNC' (Auto-selected)
├── C148 (name: 'CAP_0402', value: '100nF 6.3V 0402')
│   └── Substituted (name: 'CAP_0402', value: '100nF 6.3V 0402 X7R 10%'), by (name_pattern: 'CAP_0402', value_pattern: '100nF 6.3V 0402'), comment: 'Use X7R 10% by default'
│       └── Substituted (name: 'CAP_0402', value: '100nF 16V 0402 X7R 10%'), by (name_pattern: 'CAP_0402', value_pattern: '100nF 6.3V 0402 X7R 10%'), de-rate: 'from 6.3V to 16V'
│           └── manufacturer: 'Samsung Electro-Mechanics', mpn: 'CL05B104KO5NNNC' (Auto-selected)
├── C149 (name: 'CAP_0402', value: '100nF 6.3V 0402')
│   └── Substituted (name: 'CAP_0402', value: '100nF 6.3V 0402 X7R 10%'), by (name_pattern: 'CAP_0402', value_pattern: '100nF 6.3V 0402'), comment: 'Use X7R 10% by default'
│       └── Substituted (name: 'CAP_0402', value: '100nF 16V 0402 X7R 10%'), by (name_pattern: 'CAP_0402', value_pattern: '100nF 6.3V 0402 X7R 10%'), de-rate: 'from 6.3V to 16V'
│           └── manufacturer: 'Samsung Electro-Mechanics', mpn: 'CL05B104KO5NNNC' (Auto-selected)
├── C150 (name: 'CAP_0402', value: '100nF 6.3V 0402')
│   └── Substituted (name: 'CAP_0402', value: '100nF 6.3V 0402 X7R 10%'), by (name_pattern: 'CAP_0402', value_pattern: '100nF 6.3V 0402'), comment: 'Use X7R 10% by default'
│       └── Substituted (name: 'CAP_0402', value: '100nF 16V 0402 X7R 10%'), by (name_pattern: 'CAP_0402', value_pattern: '100nF 6.3V 0402 X7R 10%'), de-rate: 'from 6.3V to 16V'
│           └── manufacturer: 'Samsung Electro-Mechanics', mpn: 'CL05B104KO5NNNC' (Auto-selected)
├── C151 (name: 'CAP_0402', value: '100nF 6.3V 0402')
│   └── Substituted (name: 'CAP_0402', value: '100nF 6.3V 0402 X7R 10%'), by (name_pattern: 'CAP_0402', value_pattern: '100nF 6.3V 0402'), comment: 'Use X7R 10% by default'
│       └── Substituted (name: 'CAP_0402', value: '100nF 16V 0402 X7R 10%'), by (name_pattern: 'CAP_0402', value_pattern: '100nF 6.3V 0402 X7R 10%'), de-rate: 'from 6.3V to 16V'
│           └── manufacturer: 'Samsung Electro-Mechanics', mpn: 'CL05B104KO5NNNC' (Auto-selected)
├── C152 (name: 'CAP_0402', value: '100nF 6.3V 0402')
│   └── Substituted (name: 'CAP_0402', value: '100nF 6.3V 0402 X7R 10%'), by (name_pattern: 'CAP_0402', value_pattern: '100nF 6.3V 0402'), comment: 'Use X7R 10% by default'
│       └── Substituted (name: 'CAP_0402', value: '100nF 16V 0402 X7R 10%'), by (name_pattern: 'CAP_0402', value_pattern: '100nF 6.3V 0402 X7R 10%'), de-rate: 'from 6.3V to 16V'
│           └── manufacturer: 'Samsung Electro-Mechanics', mpn: 'CL05B104KO5NNNC' (Auto-selected)
├── C153 (name: 'CAP_0402', value: '100nF 6.3V 0402')
│   └── Substituted (name: 'CAP_0402', value: '100nF 6.3V 0402 X7R 10%'), by (name_pattern: 'CAP_0402', value_pattern: '100nF 6.3V 0402'), comment: 'Use X7R 10% by default'
│       └── Substituted (name: 'CAP_0402', value: '100nF 16V 0402 X7R 10%'), by (name_pattern: 'CAP_0402', value_pattern: '100nF 6.3V 0402 X7R 10%'), de-rate: 'from 6.3V to 16V'
│           └── manufacturer: 'Samsung Electro-Mechanics', mpn: 'CL05B104KO5NNNC' (Auto-selected)
├── C154 (name: 'CAP_0402', value: '100nF 6.3V 0402')
│   └── Substituted (name: 'CAP_0402', value: '100nF 6.3V 0402 X7R 10%'), by (name_pattern: 'CAP_0402', value_pattern: '100nF 6.3V 0402'), comment: 'Use X7R 10% by default'
│       └── Substituted (name: 'CAP_0402', value: '100nF 16V 0402 X7R 10%'), by (name_pattern: 'CAP_0402', value_pattern: '100nF 6.3V 0402 X7R 10%'), de-rate: 'from 6.3V to 16V'
│           └── manufacturer: 'Samsung Electro-Mechanics', mpn: 'CL05B104KO5NNNC' (Auto-selected)
├── C155 (name: 'CAP_0402', value: '100nF 6.3V 0402')
│   └── Substituted (name: 'CAP_0402', value: '100nF 6.3V 0402 X7R 10%'), by (name_pattern: 'CAP_0402', value_pattern: '100nF 6.3V 0402'), comment: 'Use X7R 10% by default'
│       └── Substituted (name: 'CAP_0402', value: '100nF 16V 0402 X7R 10%'), by (name_pattern: 'CAP_0402', value_pattern: '100nF 6.3V 0402 X7R 10%'), de-rate: 'from 6.3V to 16V'
│           └── manufacturer: 'Samsung Electro-Mechanics', mpn: 'CL05B104KO5NNNC' (Auto-selected)
├── C156 (name: 'CAP_0402', value: '100nF 6.3V 0402')
│   └── Substituted (name: 'CAP_0402', value: '100nF 6.3V 0402 X7R 10%'), by (name_pattern: 'CAP_0402', value_pattern: '100nF 6.3V 0402'), comment: 'Use X7R 10% by default'
│       └── Substituted (name: 'CAP_0402', value: '100nF 16V 0402 X7R 10%'), by (name_pattern: 'CAP_0402', value_pattern: '100nF 6.3V 0402 X7R 10%'), de-rate: 'from 6.3V to 16V'
│           └── manufacturer: 'Samsung Electro-Mechanics', mpn: 'CL05B104KO5NNNC' (Auto-selected)
├── C157 (name: 'CAP_0402', value: '1uF 6.3V 0402')
│   └── Substituted (name: 'CAP_0402', value: '1uF 6.3V 0402 X5R 10%'), by (name_pattern: 'CAP_0402', value_pattern: '1uF 6.3V 0402'), comment: 'Use X5R 10% by default'
│       └── Substituted (name: 'CAP_0402', value: '1uF 25V 0402 X5R 10%'), by (name_pattern: 'CAP_0402', value_pattern: '1uF 6.3V 0402 X5R 10%'), comment: ''
│           └── manufacturer: 'Samsung Electro-Mechanics', mpn: 'CL05A105KA5NQNC' (Auto-selected)
├── C158 (name: 'CAP_0402', value: '100nF 6.3V 0402')
│   └── Substituted (name: 'CAP_0402', value: '100nF 6.3V 0402 X7R 10%'), by (name_pattern: 'CAP_0402', value_pattern: '100nF 6.3V 0402'), comment: 'Use X7R 10% by default'
│       └── Substituted (name: 'CAP_0402', value: '100nF 16V 0402 X7R 10%'), by (name_pattern: 'CAP_0402', value_pattern: '100nF 6.3V 0402 X7R 10%'), de-rate: 'from 6.3V to 16V'
│           └── manufacturer: 'Samsung Electro-Mechanics', mpn: 'CL05B104KO5NNNC' (Auto-selected)
├── C159 (name: 'CAP_0402', value: '100nF 6.3V 0402')
│   └── Substituted (name: 'CAP_0402', value: '100nF 6.3V 0402 X7R 10%'), by (name_pattern: 'CAP_0402', value_pattern: '100nF 6.3V 0402'), comment: 'Use X7R 10% by default'
│       └── Substituted (name: 'CAP_0402', value: '100nF 16V 0402 X7R 10%'), by (name_pattern: 'CAP_0402', value_pattern: '100nF 6.3V 0402 X7R 10%'), de-rate: 'from 6.3V to 16V'
│           └── manufacturer: 'Samsung Electro-Mechanics', mpn: 'CL05B104KO5NNNC' (Auto-selected)
├── C160 (name: 'CAP_0805_N', value: '22uF 25V X5R')
│   └── Substituted (name: 'CAP_0805_N', value: '22uF 25V X5R 20%'), by (name_pattern: 'CAP_0805_N', value_pattern: '22uF 25V X5R.*'), comment: 'Use 20% by default'
│       └── manufacturer: 'Samsung Electro-Mechanics', mpn: 'CL21A226MAQNNNE' (Auto-selected)
├── C301 (name: 'CAP_0402', value: '100nF 6.3V 0402')
│   └── Substituted (name: 'CAP_0402', value: '100nF 6.3V 0402 X7R 10%'), by (name_pattern: 'CAP_0402', value_pattern: '100nF 6.3V 0402'), comment: 'Use X7R 10% by default'
│       └── Substituted (name: 'CAP_0402', value: '100nF 16V 0402 X7R 10%'), by (name_pattern: 'CAP_0402', value_pattern: '100nF 6.3V 0402 X7R 10%'), de-rate: 'from 6.3V to 16V'
│           └── manufacturer: 'Samsung Electro-Mechanics', mpn: 'CL05B104KO5NNNC' (Auto-selected)
├── C302 (name: 'CAP_0402', value: '100nF 6.3V 0402')
│   └── Substituted (name: 'CAP_0402', value: '100nF 6.3V 0402 X7R 10%'), by (name_pattern: 'CAP_0402', value_pattern: '100nF 6.3V 0402'), comment: 'Use X7R 10% by default'
│       └── Substituted (name: 'CAP_0402', value: '100nF 16V 0402 X7R 10%'), by (name_pattern: 'CAP_0402', value_pattern: '100nF 6.3V 0402 X7R 10%'), de-rate: 'from 6.3V to 16V'
│           └── manufacturer: 'Samsung Electro-Mechanics', mpn: 'CL05B104KO5NNNC' (Auto-selected)
├── C303 (name: 'CAP_0402', value: '100nF 6.3V 0402')
│   └── Substituted (name: 'CAP_0402', value: '100nF 6.3V 0402 X7R 10%'), by (name_pattern: 'CAP_0402', value_pattern: '100nF 6.3V 0402'), comment: 'Use X7R 10% by default'
│       └── Substituted (name: 'CAP_0402', value: '100nF 16V 0402 X7R 10%'), by (name_pattern: 'CAP_0402', value_pattern: '100nF 6.3V 0402 X7R 10%'), de-rate: 'from 6.3V to 16V'
│           └── manufacturer: 'Samsung Electro-Mechanics', mpn: 'CL05B104KO5NNNC' (Auto-selected)
├── C304 (name: 'CAP_0402', value: '100nF 6.3V 0402')
│   └── Substituted (name: 'CAP_0402', value: '100nF 6.3V 0402 X7R 10%'), by (name_pattern: 'CAP_0402', value_pattern: '100nF 6.3V 0402'), comment: 'Use X7R 10% by default'
│       └── Substituted (name: 'CAP_0402', value: '100nF 16V 0402 X7R 10%'), by (name_pattern: 'CAP_0402', value_pattern: '100nF 6.3V 0402 X7R 10%'), de-rate: 'from 6.3V to 16V'
│           └── manufacturer: 'Samsung Electro-Mechanics', mpn: 'CL05B104KO5NNNC' (Auto-selected)
├── C401 (name: 'CAP_0603', value: '10uF 6.3V 0603 X5R 10%')
│   └── Substituted (name: 'CAP_0603', value: '10uF 25V 0603 X5R 10%'), by (name_pattern: 'CAP_0603', value_pattern: '10uF 6.3V 0603 X5R 10%'), de-rate: 'from 6.3V to 25V'
│       └── manufacturer: 'Samsung Electro-Mechanics', mpn: 'CL10A106MA8NRNC' (Auto-selected)
├── C402 (name: 'CAP_0402', value: '100nF 6.3V 0402')
│   └── Substituted (name: 'CAP_0402', value: '100nF 6.3V 0402 X7R 10%'), by (name_pattern: 'CAP_0402', value_pattern: '100nF 6.3V 0402'), comment: 'Use X7R 10% by default'
│       └── Substituted (name: 'CAP_0402', value: '100nF 16V 0402 X7R 10%'), by (name_pattern: 'CAP_0402', value_pattern: '100nF 6.3V 0402 X7R 10%'), de-rate: 'from 6.3V to 16V'
│           └── manufacturer: 'Samsung Electro-Mechanics', mpn: 'CL05B104KO5NNNC' (Auto-selected)
├── C601 (name: 'CAP_0402', value: '1uF 6.3V 0402')
│   └── Substituted (name: 'CAP_0402', value: '1uF 6.3V 0402 X5R 10%'), by (name_pattern: 'CAP_0402', value_pattern: '1uF 6.3V 0402'), comment: 'Use X5R 10% by default'
│       └── Substituted (name: 'CAP_0402', value: '1uF 25V 0402 X5R 10%'), by (name_pattern: 'CAP_0402', value_pattern: '1uF 6.3V 0402 X5R 10%'), comment: ''
│           └── manufacturer: 'Samsung Electro-Mechanics', mpn: 'CL05A105KA5NQNC' (Auto-selected)
├── C602 (name: 'CAP_0402', value: '1uF 6.3V 0402')
│   └── Substituted (name: 'CAP_0402', value: '1uF 6.3V 0402 X5R 10%'), by (name_pattern: 'CAP_0402', value_pattern: '1uF 6.3V 0402'), comment: 'Use X5R 10% by default'
│       └── Substituted (name: 'CAP_0402', value: '1uF 25V 0402 X5R 10%'), by (name_pattern: 'CAP_0402', value_pattern: '1uF 6.3V 0402 X5R 10%'), comment: ''
│           └── manufacturer: 'Samsung Electro-Mechanics', mpn: 'CL05A105KA5NQNC' (Auto-selected)
├── C603 (name: 'CAP_0402', value: '100nF 6.3V 0402')
│   └── Substituted (name: 'CAP_0402', value: '100nF 6.3V 0402 X7R 10%'), by (name_pattern: 'CAP_0402', value_pattern: '100nF 6.3V 0402'), comment: 'Use X7R 10% by default'
│       └── Substituted (name: 'CAP_0402', value: '100nF 16V 0402 X7R 10%'), by (name_pattern: 'CAP_0402', value_pattern: '100nF 6.3V 0402 X7R 10%'), de-rate: 'from 6.3V to 16V'
│           └── manufacturer: 'Samsung Electro-Mechanics', mpn: 'CL05B104KO5NNNC' (Auto-selected)
├── C604 (name: 'CAP_0402', value: '100nF 6.3V 0402')
│   └── Substituted (name: 'CAP_0402', value: '100nF 6.3V 0402 X7R 10%'), by (name_pattern: 'CAP_0402', value_pattern: '100nF 6.3V 0402'), comment: 'Use X7R 10% by default'
│       └── Substituted (name: 'CAP_0402', value: '100nF 16V 0402 X7R 10%'), by (name_pattern: 'CAP_0402', value_pattern: '100nF 6.3V 0402 X7R 10%'), de-rate: 'from 6.3V to 16V'
│           └── manufacturer: 'Samsung Electro-Mechanics', mpn: 'CL05B104KO5NNNC' (Auto-selected)
├── D1 (name: 'LED 0603 BLUE', value: '3V3')
│   └── Substituted (name: 'LED_0603', value: 'BLUE'), by (name_pattern: 'LED 0603 BLUE', value_pattern: '.*'), comment: ''
│       └── manufacturer: 'Foshan NationStar Optoelectronics', mpn: 'NCD0603B1' (Auto-selected)
├── D2 (name: 'LED 0603 BLUE', value: '3V3_ESP32')
│   └── Substituted (name: 'LED_0603', value: 'BLUE'), by (name_pattern: 'LED 0603 BLUE', value_pattern: '.*'), comment: ''
│       └── manufacturer: 'Foshan NationStar Optoelectronics', mpn: 'NCD0603B1' (Auto-selected)
├── D101 (name: 'LED 0603 GREEN', value: 'CDONE')
│   └── Substituted (name: 'LED_0603', value: 'GREEN'), by (name_pattern: 'LED 0603 GREEN', value_pattern: '.*'), comment: ''
│       └── manufacturer: 'Foshan NationStar Optoelectronics', mpn: 'NCD0603G1' (Auto-selected)
├── D102 (name: 'BAV21W', value: '')
│   └── manufacturer: 'MDD(Microdiode Semiconductor)', mpn: 'BAV21W' (Auto-selected)
├── D103 (name: 'LED 0603 RED', value: 'MCU_ACT')
│   └── Substituted (name: 'LED_0603', value: 'RED'), by (name_pattern: 'LED 0603 RED', value_pattern: '.*'), comment: ''
│       └── manufacturer: 'Foshan NationStar Optoelectronics', mpn: 'NCD0603R5' (Auto-selected)
├── D104 (name: 'LED 0603 ORANGE', value: 'ESP_ACT')
│   └── Substituted (name: 'LED_0603', value: 'ORANGE'), by (name_pattern: 'LED 0603 ORANGE', value_pattern: '.*'), comment: ''
│       └── manufacturer: 'Foshan NationStar Optoelectronics', mpn: 'NCD0603O1' (Auto-selected)
├── D105 (name: 'LED 0603 YELLOW', value: 'FPGA_ACT')
│   └── Substituted (name: 'LED_0603', value: 'YELLOW'), by (name_pattern: 'LED 0603 YELLOW', value_pattern: '.*'), comment: ''
│       └── manufacturer: 'Foshan NationStar Optoelectronics', mpn: 'NCD0603Y1' (Auto-selected)
├── D601 (name: 'LED 0603 GREEN', value: 'CDONE')
│   └── Substituted (name: 'LED_0603', value: 'GREEN'), by (name_pattern: 'LED 0603 GREEN', value_pattern: '.*'), comment: ''
│       └── manufacturer: 'Foshan NationStar Optoelectronics', mpn: 'NCD0603G1' (Auto-selected)
├── D602 (name: 'LED 0603 GREEN', value: 'CDONE')
│   └── Substituted (name: 'LED_0603', value: 'GREEN'), by (name_pattern: 'LED 0603 GREEN', value_pattern: '.*'), comment: ''
│       └── manufacturer: 'Foshan NationStar Optoelectronics', mpn: 'NCD0603G1' (Auto-selected)
├── J1 (name: 'B2B-XH-A(LF)(SN)', value: 'AIN1')
│   └── Substituted (name: 'GT-A2501WVD-102SBT01', value: ''), by (name_pattern: 'B2B-XH-A(LF)(SN)', value_pattern: '.*'), comment: 'Use g-switch brand instead'
│       └── manufacturer: 'G-Switch', mpn: 'GT-A2501WVD-102SBT01' (Auto-selected)
├── J402 (name: 'FTSH-105-01-X-DV-P-K-X', value: 'DEBUG')
│   └── Substituted (name: 'FTSH-105-01-L-DV-K-P-TR', value: ''), by (name_pattern: 'FTSH-105-01-X-DV-P-K-X', value_pattern: '.*'), comment: 'Use different variant'
│       └── manufacturer: 'Samtec', mpn: 'FTSH-105-01-L-DV-K-P-TR' (Auto-selected)
├── J403 (name: 'LPPB112NFSS-RC', value: 'LA2_IO')
│   └── Substituted (name: 'PM127-2-11-S-4.3', value: ''), by (name_pattern: 'LPPB112NFSS-RC', value_pattern: '.*'), comment: 'Use HCTL brand instead'
│       └── manufacturer: 'HCTL', mpn: 'PM127-2-11-S-4.3' (Auto-selected)
├── J404 (name: '10164228-1001A1RLF', value: '')
│   └── Substituted (name: 'X0408WVS-100A-LPV01', value: ''), by (name_pattern: '10164228-1001A1RLF', value_pattern: '.*'), comment: 'Use XKB Connection brand instead'
│       └── manufacturer: 'XKB Connection', mpn: 'X0408WVS-100A-LPV01' (Auto-selected)
├── J405 (name: 'LPPB112NFSS-RC', value: 'LA2_IO')
│   └── Substituted (name: 'PM127-2-11-S-4.3', value: ''), by (name_pattern: 'LPPB112NFSS-RC', value_pattern: '.*'), comment: 'Use HCTL brand instead'
│       └── manufacturer: 'HCTL', mpn: 'PM127-2-11-S-4.3' (Auto-selected)
├── J406 (name: '10164228-1001A1RLF', value: '')
│   └── Substituted (name: 'X0408WVS-100A-LPV01', value: ''), by (name_pattern: '10164228-1001A1RLF', value_pattern: '.*'), comment: 'Use XKB Connection brand instead'
│       └── manufacturer: 'XKB Connection', mpn: 'X0408WVS-100A-LPV01' (Auto-selected)
├── J407 (name: 'PK-47309-375', value: '')
│   └── Substituted (name: 'LCK-TF-027H37508-WLG', value: ''), by (name_pattern: 'PK-47309-375', value_pattern: '.*'), comment: 'Use LCKELEC brand instead'
│       └── manufacturer: 'LCKELEC', mpn: 'LCK-TF-027H37508-WLG' (Auto-selected)
├── J408 (name: 'LPPB112NFSS-RC', value: 'LA2_IO')
│   └── Substituted (name: 'PM127-2-11-S-4.3', value: ''), by (name_pattern: 'LPPB112NFSS-RC', value_pattern: '.*'), comment: 'Use HCTL brand instead'
│       └── manufacturer: 'HCTL', mpn: 'PM127-2-11-S-4.3' (Auto-selected)
├── J409 (name: '10164228-1001A1RLF', value: '')
│   └── Substituted (name: 'X0408WVS-100A-LPV01', value: ''), by (name_pattern: '10164228-1001A1RLF', value_pattern: '.*'), comment: 'Use XKB Connection brand instead'
│       └── manufacturer: 'XKB Connection', mpn: 'X0408WVS-100A-LPV01' (Auto-selected)
├── J410 (name: 'FTS-102-01-L-DV', value: '')
│   └── manufacturer: 'HCTL', mpn: 'PZ127-2-02-S' (Auto-selected)
├── J411 (name: '10164228-1001A1RLF', value: '')
│   └── Substituted (name: 'X0408WVS-100A-LPV01', value: ''), by (name_pattern: '10164228-1001A1RLF', value_pattern: '.*'), comment: 'Use XKB Connection brand instead'
│       └── manufacturer: 'XKB Connection', mpn: 'X0408WVS-100A-LPV01' (Auto-selected)
├── J601 (name: 'TYPE-C 16PLT-H10.0', value: '')
│   └── manufacturer: 'SHOU HAN', mpn: 'TYPE-C 16PLT-H10.0' (Auto-selected)
├── J602 (name: 'TYPE-C 16PLT-H10.0', value: '')
│   └── manufacturer: 'SHOU HAN', mpn: 'TYPE-C 16PLT-H10.0' (Auto-selected)
├── L1 (name: 'DFE252012F-1R0M', value: '1uH')
│   └── manufacturer: 'muRata', mpn: 'DFE252012F-1R0M=P2' (Auto-selected)
├── L2 (name: 'DFE252012F-1R0M', value: '1uH')
│   └── manufacturer: 'muRata', mpn: 'DFE252012F-1R0M=P2' (Auto-selected)
├── L3 (name: 'DFE252012F-1R0M', value: '1uH')
│   └── manufacturer: 'muRata', mpn: 'DFE252012F-1R0M=P2' (Auto-selected)
├── L101 (name: 'IND_0603_N', value: '2.2uH 20% 1.8A 0.237ohm')
│   └── manufacturer: 'Taiyo Yuden', mpn: 'MCHK1608T2R2MKN' (Auto-selected)
├── R1 (name: 'RES_1206_N', value: '0R 1206')
│   └── Substituted (name: 'RES_1206_N', value: '0R 1206 500mW 200V'), by (name_pattern: 'RES_1206_N', value_pattern: '0R 1206'), comment: 'Use 500mW by default', comment: 'Use 200V by default'
│       └── manufacturer: 'UNI-ROYAL(Uniroyal Elec)', mpn: 'HP06W2J0000T5E' (Auto-selected)
├── R2 (name: 'RES_0402', value: '220R 0402 1%')
│   └── Substituted (name: 'RES_0402', value: '220R 0402 1% 50V'), by (name_pattern: 'RES_0402', value_pattern: '220R 0402 1%'), comment: 'Use 50V by default'
│       └── manufacturer: 'UNI-ROYAL(Uniroyal Elec)', mpn: '0402WGF2200TCE' (Auto-selected)
├── R3 (name: 'RES_0402', value: '220R 0402 1%')
│   └── Substituted (name: 'RES_0402', value: '220R 0402 1% 50V'), by (name_pattern: 'RES_0402', value_pattern: '220R 0402 1%'), comment: 'Use 50V by default'
│       └── manufacturer: 'UNI-ROYAL(Uniroyal Elec)', mpn: '0402WGF2200TCE' (Auto-selected)
├── R4 (name: 'RES_0402', value: '10K 0402 1%')
│   └── Substituted (name: 'RES_0402', value: '10K 0402 1% 50V'), by (name_pattern: 'RES_0402', value_pattern: '10K 0402 1%'), comment: 'Use 50V by default'
│       └── manufacturer: 'UNI-ROYAL(Uniroyal Elec)', mpn: '0402WGF1002TCE' (Auto-selected)
├── R5 (name: 'RES_0402', value: '10K 0402 1%')
│   └── Substituted (name: 'RES_0402', value: '10K 0402 1% 50V'), by (name_pattern: 'RES_0402', value_pattern: '10K 0402 1%'), comment: 'Use 50V by default'
│       └── manufacturer: 'UNI-ROYAL(Uniroyal Elec)', mpn: '0402WGF1002TCE' (Auto-selected)
├── R6 (name: 'RES_0402', value: '453K')
│   └── Substituted (name: 'RES_0402', value: '453K 0402 1%'), by (name_pattern: 'RES_0402', value_pattern: '453K'), comment: 'Use 1% by default'
│       └── Substituted (name: 'RES_0402', value: '453K 0402 1% 50V'), by (name_pattern: 'RES_0402', value_pattern: '453K 0402 1%'), comment: 'Use 50V by default'
│           └── manufacturer: 'UNI-ROYAL(Uniroyal Elec)', mpn: '0402WGF4533TCE' (Auto-selected)
├── R7 (name: 'RES_0402', value: '100K')
│   └── Substituted (name: 'RES_0402', value: '100K 0402 1%'), by (name_pattern: 'RES_0402', value_pattern: '100K'), comment: 'Use 1% by default'
│       └── Substituted (name: 'RES_0402', value: '100K 0402 1% 50V'), by (name_pattern: 'RES_0402', value_pattern: '100K 0402 1%'), comment: 'Use 50V by default'
│           └── manufacturer: 'UNI-ROYAL(Uniroyal Elec)', mpn: '0402WGF1003TCE' (Auto-selected)
├── R8 (name: 'RES_0402', value: '100K')
│   └── Substituted (name: 'RES_0402', value: '100K 0402 1%'), by (name_pattern: 'RES_0402', value_pattern: '100K'), comment: 'Use 1% by default'
│       └── Substituted (name: 'RES_0402', value: '100K 0402 1% 50V'), by (name_pattern: 'RES_0402', value_pattern: '100K 0402 1%'), comment: 'Use 50V by default'
│           └── manufacturer: 'UNI-ROYAL(Uniroyal Elec)', mpn: '0402WGF1003TCE' (Auto-selected)
├── R9 (name: 'RES_0402', value: '453K')
│   └── Substituted (name: 'RES_0402', value: '453K 0402 1%'), by (name_pattern: 'RES_0402', value_pattern: '453K'), comment: 'Use 1% by default'
│       └── Substituted (name: 'RES_0402', value: '453K 0402 1% 50V'), by (name_pattern: 'RES_0402', value_pattern: '453K 0402 1%'), comment: 'Use 50V by default'
│           └── manufacturer: 'UNI-ROYAL(Uniroyal Elec)', mpn: '0402WGF4533TCE' (Auto-selected)
├── R10 (name: 'RES_0402', value: '453K')
│   └── Substituted (name: 'RES_0402', value: '453K 0402 1%'), by (name_pattern: 'RES_0402', value_pattern: '453K'), comment: 'Use 1% by default'
│       └── Substituted (name: 'RES_0402', value: '453K 0402 1% 50V'), by (name_pattern: 'RES_0402', value_pattern: '453K 0402 1%'), comment: 'Use 50V by default'
│           └── manufacturer: 'UNI-ROYAL(Uniroyal Elec)', mpn: '0402WGF4533TCE' (Auto-selected)
├── R11 (name: 'RES_0402', value: '100K')
│   └── Substituted (name: 'RES_0402', value: '100K 0402 1%'), by (name_pattern: 'RES_0402', value_pattern: '100K'), comment: 'Use 1% by default'
│       └── Substituted (name: 'RES_0402', value: '100K 0402 1% 50V'), by (name_pattern: 'RES_0402', value_pattern: '100K 0402 1%'), comment: 'Use 50V by default'
│           └── manufacturer: 'UNI-ROYAL(Uniroyal Elec)', mpn: '0402WGF1003TCE' (Auto-selected)
├── R12 (name: 'RES_0402', value: '453K')
│   └── Substituted (name: 'RES_0402', value: '453K 0402 1%'), by (name_pattern: 'RES_0402', value_pattern: '453K'), comment: 'Use 1% by default'
│       └── Substituted (name: 'RES_0402', value: '453K 0402 1% 50V'), by (name_pattern: 'RES_0402', value_pattern: '453K 0402 1%'), comment: 'Use 50V by default'
│           └── manufacturer: 'UNI-ROYAL(Uniroyal Elec)', mpn: '0402WGF4533TCE' (Auto-selected)
├── R13 (name: 'RES_0402', value: '453K')
│   └── Substituted (name: 'RES_0402', value: '453K 0402 1%'), by (name_pattern: 'RES_0402', value_pattern: '453K'), comment: 'Use 1% by default'
│       └── Substituted (name: 'RES_0402', value: '453K 0402 1% 50V'), by (name_pattern: 'RES_0402', value_pattern: '453K 0402 1%'), comment: 'Use 50V by default'
│           └── manufacturer: 'UNI-ROYAL(Uniroyal Elec)', mpn: '0402WGF4533TCE' (Auto-selected)
├── R14 (name: 'RES_0402', value: '100K')
│   └── Substituted (name: 'RES_0402', value: '100K 0402 1%'), by (name_pattern: 'RES_0402', value_pattern: '100K'), comment: 'Use 1% by default'
│       └── Substituted (name: 'RES_0402', value: '100K 0402 1% 50V'), by (name_pattern: 'RES_0402', value_pattern: '100K 0402 1%'), comment: 'Use 50V by default'
│           └── manufacturer: 'UNI-ROYAL(Uniroyal Elec)', mpn: '0402WGF1003TCE' (Auto-selected)
├── R101 (name: 'RES_0402', value: '10K 0402 1%')
│   └── Substituted (name: 'RES_0402', value: '10K 0402 1% 50V'), by (name_pattern: 'RES_0402', value_pattern: '10K 0402 1%'), comment: 'Use 50V by default'
│       └── manufacturer: 'UNI-ROYAL(Uniroyal Elec)', mpn: '0402WGF1002TCE' (Auto-selected)
├── R102 (name: 'RES_0402', value: '0R')
│   └── Substituted (name: 'RES_0402', value: '0R 0402 50V'), by (name_pattern: 'RES_0402', value_pattern: '0R'), comment: 'Use 50V by default'
│       └── manufacturer: 'UNI-ROYAL(Uniroyal Elec)', mpn: '0402WGF0000TCE' (Auto-selected)
├── R103 (name: 'RES_0402', value: '0R')
│   └── Substituted (name: 'RES_0402', value: '0R 0402 50V'), by (name_pattern: 'RES_0402', value_pattern: '0R'), comment: 'Use 50V by default'
│       └── manufacturer: 'UNI-ROYAL(Uniroyal Elec)', mpn: '0402WGF0000TCE' (Auto-selected)
├── R104 (name: 'RES_0402', value: '47R')
│   └── Substituted (name: 'RES_0402', value: '47R 0402 1%'), by (name_pattern: 'RES_0402', value_pattern: '47R'), comment: 'Use 1% by default'
│       └── Substituted (name: 'RES_0402', value: '47R 0402 1% 50V'), by (name_pattern: 'RES_0402', value_pattern: '47R 0402 1%'), comment: 'Use 50V by default'
│           └── manufacturer: 'UNI-ROYAL(Uniroyal Elec)', mpn: '0402WGF470JTCE' (Auto-selected)
├── R105 (name: 'RES_0402', value: '330R 0402 1%')
│   └── Substituted (name: 'RES_0402', value: '330R 0402 1% 50V'), by (name_pattern: 'RES_0402', value_pattern: '330R 0402 1%'), comment: 'Use 50V by default'
│       └── manufacturer: 'UNI-ROYAL(Uniroyal Elec)', mpn: '0402WGF3300TCE' (Auto-selected)
├── R106 (name: 'RES_0402', value: '330R 0402 1%')
│   └── Substituted (name: 'RES_0402', value: '330R 0402 1% 50V'), by (name_pattern: 'RES_0402', value_pattern: '330R 0402 1%'), comment: 'Use 50V by default'
│       └── manufacturer: 'UNI-ROYAL(Uniroyal Elec)', mpn: '0402WGF3300TCE' (Auto-selected)
├── R107 (name: 'RES_0402', value: '10K 0402 1%')
│   └── Substituted (name: 'RES_0402', value: '10K 0402 1% 50V'), by (name_pattern: 'RES_0402', value_pattern: '10K 0402 1%'), comment: 'Use 50V by default'
│       └── manufacturer: 'UNI-ROYAL(Uniroyal Elec)', mpn: '0402WGF1002TCE' (Auto-selected)
├── R108 (name: 'RES_0603_N', value: '100R')
│   └── Substituted (name: 'RES_0603_N', value: '100R 0603 1%'), by (name_pattern: 'RES_0603_N', value_pattern: '100R'), comment: 'Use 1% by default'
│       └── Substituted (name: 'RES_0603_N', value: '100R 0603 1% 75V'), by (name_pattern: 'RES_0603_N', value_pattern: '100R 0603 1%'), comment: 'Use 75V by default'
│           └── manufacturer: 'UNI-ROYAL(Uniroyal Elec)', mpn: '0603WAF1000T5E' (Auto-selected)
├── R109 (name: 'RES_0402', value: '10K 0402 1%')
│   └── Substituted (name: 'RES_0402', value: '10K 0402 1% 50V'), by (name_pattern: 'RES_0402', value_pattern: '10K 0402 1%'), comment: 'Use 50V by default'
│       └── manufacturer: 'UNI-ROYAL(Uniroyal Elec)', mpn: '0402WGF1002TCE' (Auto-selected)
├── R110 (name: 'RES_0603_N', value: '100R')
│   └── Substituted (name: 'RES_0603_N', value: '100R 0603 1%'), by (name_pattern: 'RES_0603_N', value_pattern: '100R'), comment: 'Use 1% by default'
│       └── Substituted (name: 'RES_0603_N', value: '100R 0603 1% 75V'), by (name_pattern: 'RES_0603_N', value_pattern: '100R 0603 1%'), comment: 'Use 75V by default'
│           └── manufacturer: 'UNI-ROYAL(Uniroyal Elec)', mpn: '0603WAF1000T5E' (Auto-selected)
├── R111 (name: 'RES_0603_N', value: '100R')
│   └── Substituted (name: 'RES_0603_N', value: '100R 0603 1%'), by (name_pattern: 'RES_0603_N', value_pattern: '100R'), comment: 'Use 1% by default'
│       └── Substituted (name: 'RES_0603_N', value: '100R 0603 1% 75V'), by (name_pattern: 'RES_0603_N', value_pattern: '100R 0603 1%'), comment: 'Use 75V by default'
│           └── manufacturer: 'UNI-ROYAL(Uniroyal Elec)', mpn: '0603WAF1000T5E' (Auto-selected)
├── R112 (name: 'RES_0402', value: '10K 0402 1%')
│   └── Substituted (name: 'RES_0402', value: '10K 0402 1% 50V'), by (name_pattern: 'RES_0402', value_pattern: '10K 0402 1%'), comment: 'Use 50V by default'
│       └── manufacturer: 'UNI-ROYAL(Uniroyal Elec)', mpn: '0402WGF1002TCE' (Auto-selected)
├── R113 (name: 'RES_0402', value: '10K 0402 1%')
│   └── Substituted (name: 'RES_0402', value: '10K 0402 1% 50V'), by (name_pattern: 'RES_0402', value_pattern: '10K 0402 1%'), comment: 'Use 50V by default'
│       └── manufacturer: 'UNI-ROYAL(Uniroyal Elec)', mpn: '0402WGF1002TCE' (Auto-selected)
├── R114 (name: 'RES_0603_N', value: '1R 0603')
│   └── Substituted (name: 'RES_0603_N', value: '1R 0603 1%'), by (name_pattern: 'RES_0603_N', value_pattern: '1R 0603'), comment: 'Use 1% by default'
│       └── Substituted (name: 'RES_0603_N', value: '1R 0603 1% 75V'), by (name_pattern: 'RES_0603_N', value_pattern: '1R 0603 1%'), comment: 'Use 75V by default'
│           └── manufacturer: 'UNI-ROYAL(Uniroyal Elec)', mpn: '0603WAF100KT5E' (Auto-selected)
├── R115 (name: 'RES_0603_N', value: '1R 0603')
│   └── Substituted (name: 'RES_0603_N', value: '1R 0603 1%'), by (name_pattern: 'RES_0603_N', value_pattern: '1R 0603'), comment: 'Use 1% by default'
│       └── Substituted (name: 'RES_0603_N', value: '1R 0603 1% 75V'), by (name_pattern: 'RES_0603_N', value_pattern: '1R 0603 1%'), comment: 'Use 75V by default'
│           └── manufacturer: 'UNI-ROYAL(Uniroyal Elec)', mpn: '0603WAF100KT5E' (Auto-selected)
├── R116 (name: 'RES_0402', value: '10K 0402 1%')
│   └── Substituted (name: 'RES_0402', value: '10K 0402 1% 50V'), by (name_pattern: 'RES_0402', value_pattern: '10K 0402 1%'), comment: 'Use 50V by default'
│       └── manufacturer: 'UNI-ROYAL(Uniroyal Elec)', mpn: '0402WGF1002TCE' (Auto-selected)
├── R117 (name: 'RES_0402', value: '10K 0402 1%')
│   └── Substituted (name: 'RES_0402', value: '10K 0402 1% 50V'), by (name_pattern: 'RES_0402', value_pattern: '10K 0402 1%'), comment: 'Use 50V by default'
│       └── manufacturer: 'UNI-ROYAL(Uniroyal Elec)', mpn: '0402WGF1002TCE' (Auto-selected)
├── R118 (name: 'RES_0402', value: '33R 0402 1%')
│   └── Substituted (name: 'RES_0402', value: '33R 0402 1% 50V'), by (name_pattern: 'RES_0402', value_pattern: '33R 0402 1%'), comment: 'Use 50V by default'
│       └── manufacturer: 'UNI-ROYAL(Uniroyal Elec)', mpn: '0402WGF330JTCE' (Auto-selected)
├── R119 (name: 'RES_0402', value: '33R 0402 1%')
│   └── Substituted (name: 'RES_0402', value: '33R 0402 1% 50V'), by (name_pattern: 'RES_0402', value_pattern: '33R 0402 1%'), comment: 'Use 50V by default'
│       └── manufacturer: 'UNI-ROYAL(Uniroyal Elec)', mpn: '0402WGF330JTCE' (Auto-selected)
├── R120 (name: 'RES_0402', value: '33R 0402 1%')
│   └── Substituted (name: 'RES_0402', value: '33R 0402 1% 50V'), by (name_pattern: 'RES_0402', value_pattern: '33R 0402 1%'), comment: 'Use 50V by default'
│       └── manufacturer: 'UNI-ROYAL(Uniroyal Elec)', mpn: '0402WGF330JTCE' (Auto-selected)
├── R121 (name: 'RES_0402', value: '10K 0402 1%')
│   └── Substituted (name: 'RES_0402', value: '10K 0402 1% 50V'), by (name_pattern: 'RES_0402', value_pattern: '10K 0402 1%'), comment: 'Use 50V by default'
│       └── manufacturer: 'UNI-ROYAL(Uniroyal Elec)', mpn: '0402WGF1002TCE' (Auto-selected)
├── R122 (name: 'RES_0402', value: '10K 0402 1%')
│   └── Substituted (name: 'RES_0402', value: '10K 0402 1% 50V'), by (name_pattern: 'RES_0402', value_pattern: '10K 0402 1%'), comment: 'Use 50V by default'
│       └── manufacturer: 'UNI-ROYAL(Uniroyal Elec)', mpn: '0402WGF1002TCE' (Auto-selected)
├── R123 (name: 'RES_0402', value: '33R 0402 1%')
│   └── Substituted (name: 'RES_0402', value: '33R 0402 1% 50V'), by (name_pattern: 'RES_0402', value_pattern: '33R 0402 1%'), comment: 'Use 50V by default'
│       └── manufacturer: 'UNI-ROYAL(Uniroyal Elec)', mpn: '0402WGF330JTCE' (Auto-selected)
├── R124 (name: 'RES_0402', value: '33R 0402 1%')
│   └── Substituted (name: 'RES_0402', value: '33R 0402 1% 50V'), by (name_pattern: 'RES_0402', value_pattern: '33R 0402 1%'), comment: 'Use 50V by default'
│       └── manufacturer: 'UNI-ROYAL(Uniroyal Elec)', mpn: '0402WGF330JTCE' (Auto-selected)
├── R125 (name: 'RES_0402', value: '10K 0402 1%')
│   └── Substituted (name: 'RES_0402', value: '10K 0402 1% 50V'), by (name_pattern: 'RES_0402', value_pattern: '10K 0402 1%'), comment: 'Use 50V by default'
│       └── manufacturer: 'UNI-ROYAL(Uniroyal Elec)', mpn: '0402WGF1002TCE' (Auto-selected)
├── R126 (name: 'RES_0603_N', value: '1R 0603')
│   └── Substituted (name: 'RES_0603_N', value: '1R 0603 1%'), by (name_pattern: 'RES_0603_N', value_pattern: '1R 0603'), comment: 'Use 1% by default'
│       └── Substituted (name: 'RES_0603_N', value: '1R 0603 1% 75V'), by (name_pattern: 'RES_0603_N', value_pattern: '1R 0603 1%'), comment: 'Use 75V by default'
│           └── manufacturer: 'UNI-ROYAL(Uniroyal Elec)', mpn: '0603WAF100KT5E' (Auto-selected)
├── R127 (name: 'RES_0603_N', value: '1R 0603')
│   └── Substituted (name: 'RES_0603_N', value: '1R 0603 1%'), by (name_pattern: 'RES_0603_N', value_pattern: '1R 0603'), comment: 'Use 1% by default'
│       └── Substituted (name: 'RES_0603_N', value: '1R 0603 1% 75V'), by (name_pattern: 'RES_0603_N', value_pattern: '1R 0603 1%'), comment: 'Use 75V by default'
│           └── manufacturer: 'UNI-ROYAL(Uniroyal Elec)', mpn: '0603WAF100KT5E' (Auto-selected)
├── R128 (name: 'RES_0402', value: '10K 0402 1%')
│   └── Substituted (name: 'RES_0402', value: '10K 0402 1% 50V'), by (name_pattern: 'RES_0402', value_pattern: '10K 0402 1%'), comment: 'Use 50V by default'
│       └── manufacturer: 'UNI-ROYAL(Uniroyal Elec)', mpn: '0402WGF1002TCE' (Auto-selected)
├── R129 (name: 'RES_0402', value: '10K 0402 1%')
│   └── Substituted (name: 'RES_0402', value: '10K 0402 1% 50V'), by (name_pattern: 'RES_0402', value_pattern: '10K 0402 1%'), comment: 'Use 50V by default'
│       └── manufacturer: 'UNI-ROYAL(Uniroyal Elec)', mpn: '0402WGF1002TCE' (Auto-selected)
├── R130 (name: 'RES_0402', value: '33R 0402 1%')
│   └── Substituted (name: 'RES_0402', value: '33R 0402 1% 50V'), by (name_pattern: 'RES_0402', value_pattern: '33R 0402 1%'), comment: 'Use 50V by default'
│       └── manufacturer: 'UNI-ROYAL(Uniroyal Elec)', mpn: '0402WGF330JTCE' (Auto-selected)
├── R131 (name: 'RES_0402', value: '10K 0402 1%')
│   └── Substituted (name: 'RES_0402', value: '10K 0402 1% 50V'), by (name_pattern: 'RES_0402', value_pattern: '10K 0402 1%'), comment: 'Use 50V by default'
│       └── manufacturer: 'UNI-ROYAL(Uniroyal Elec)', mpn: '0402WGF1002TCE' (Auto-selected)
├── R132 (name: 'RES_0402', value: '33R 0402 1%')
│   └── Substituted (name: 'RES_0402', value: '33R 0402 1% 50V'), by (name_pattern: 'RES_0402', value_pattern: '33R 0402 1%'), comment: 'Use 50V by default'
│       └── manufacturer: 'UNI-ROYAL(Uniroyal Elec)', mpn: '0402WGF330JTCE' (Auto-selected)
├── R133 (name: 'RES_0402', value: '33R 0402 1%')
│   └── Substituted (name: 'RES_0402', value: '33R 0402 1% 50V'), by (name_pattern: 'RES_0402', value_pattern: '33R 0402 1%'), comment: 'Use 50V by default'
│       └── manufacturer: 'UNI-ROYAL(Uniroyal Elec)', mpn: '0402WGF330JTCE' (Auto-selected)
├── R134 (name: 'RES_0402', value: '330R 0402 1%')
│   └── Substituted (name: 'RES_0402', value: '330R 0402 1% 50V'), by (name_pattern: 'RES_0402', value_pattern: '330R 0402 1%'), comment: 'Use 50V by default'
│       └── manufacturer: 'UNI-ROYAL(Uniroyal Elec)', mpn: '0402WGF3300TCE' (Auto-selected)
├── R135 (name: 'RES_0402', value: '33R 0402 1%')
│   └── Substituted (name: 'RES_0402', value: '33R 0402 1% 50V'), by (name_pattern: 'RES_0402', value_pattern: '33R 0402 1%'), comment: 'Use 50V by default'
│       └── manufacturer: 'UNI-ROYAL(Uniroyal Elec)', mpn: '0402WGF330JTCE' (Auto-selected)
├── R136 (name: 'RES_0402', value: '33R 0402 1%')
│   └── Substituted (name: 'RES_0402', value: '33R 0402 1% 50V'), by (name_pattern: 'RES_0402', value_pattern: '33R 0402 1%'), comment: 'Use 50V by default'
│       └── manufacturer: 'UNI-ROYAL(Uniroyal Elec)', mpn: '0402WGF330JTCE' (Auto-selected)
├── R137 (name: 'RES_0402', value: '330R 0402 1%')
│   └── Substituted (name: 'RES_0402', value: '330R 0402 1% 50V'), by (name_pattern: 'RES_0402', value_pattern: '330R 0402 1%'), comment: 'Use 50V by default'
│       └── manufacturer: 'UNI-ROYAL(Uniroyal Elec)', mpn: '0402WGF3300TCE' (Auto-selected)
├── R138 (name: 'RES_0402', value: '330R 0402 1%')
│   └── Substituted (name: 'RES_0402', value: '330R 0402 1% 50V'), by (name_pattern: 'RES_0402', value_pattern: '330R 0402 1%'), comment: 'Use 50V by default'
│       └── manufacturer: 'UNI-ROYAL(Uniroyal Elec)', mpn: '0402WGF3300TCE' (Auto-selected)
├── R139 (name: 'RES_0402', value: '330R 0402 1%')
│   └── Substituted (name: 'RES_0402', value: '330R 0402 1% 50V'), by (name_pattern: 'RES_0402', value_pattern: '330R 0402 1%'), comment: 'Use 50V by default'
│       └── manufacturer: 'UNI-ROYAL(Uniroyal Elec)', mpn: '0402WGF3300TCE' (Auto-selected)
├── R401 (name: 'RES_0603_N', value: '100R')
│   └── Substituted (name: 'RES_0603_N', value: '100R 0603 1%'), by (name_pattern: 'RES_0603_N', value_pattern: '100R'), comment: 'Use 1% by default'
│       └── Substituted (name: 'RES_0603_N', value: '100R 0603 1% 75V'), by (name_pattern: 'RES_0603_N', value_pattern: '100R 0603 1%'), comment: 'Use 75V by default'
│           └── manufacturer: 'UNI-ROYAL(Uniroyal Elec)', mpn: '0603WAF1000T5E' (Auto-selected)
├── R402 (name: 'RES_0402', value: '10K 0402 1%')
│   └── Substituted (name: 'RES_0402', value: '10K 0402 1% 50V'), by (name_pattern: 'RES_0402', value_pattern: '10K 0402 1%'), comment: 'Use 50V by default'
│       └── manufacturer: 'UNI-ROYAL(Uniroyal Elec)', mpn: '0402WGF1002TCE' (Auto-selected)
├── R403 (name: 'YC164-FR-072KL', value: '2K')
│   └── manufacturer: 'YAGEO', mpn: 'YC164-FR-072KL' (Auto-selected)
├── R404 (name: 'RES_0402', value: '10K 0402 1%')
│   └── Substituted (name: 'RES_0402', value: '10K 0402 1% 50V'), by (name_pattern: 'RES_0402', value_pattern: '10K 0402 1%'), comment: 'Use 50V by default'
│       └── manufacturer: 'UNI-ROYAL(Uniroyal Elec)', mpn: '0402WGF1002TCE' (Auto-selected)
├── R405 (name: 'RES_0402', value: '0R')
│   └── Substituted (name: 'RES_0402', value: '0R 0402 50V'), by (name_pattern: 'RES_0402', value_pattern: '0R'), comment: 'Use 50V by default'
│       └── manufacturer: 'UNI-ROYAL(Uniroyal Elec)', mpn: '0402WGF0000TCE' (Auto-selected)
├── R406 (name: 'RES_0402', value: '0R')
│   └── Substituted (name: 'RES_0402', value: '0R 0402 50V'), by (name_pattern: 'RES_0402', value_pattern: '0R'), comment: 'Use 50V by default'
│       └── manufacturer: 'UNI-ROYAL(Uniroyal Elec)', mpn: '0402WGF0000TCE' (Auto-selected)
├── R407 (name: 'RES_0402', value: '10K 0402 1%')
│   └── Substituted (name: 'RES_0402', value: '10K 0402 1% 50V'), by (name_pattern: 'RES_0402', value_pattern: '10K 0402 1%'), comment: 'Use 50V by default'
│       └── manufacturer: 'UNI-ROYAL(Uniroyal Elec)', mpn: '0402WGF1002TCE' (Auto-selected)
├── R408 (name: 'RES_0402', value: '10K 0402 1%')
│   └── Substituted (name: 'RES_0402', value: '10K 0402 1% 50V'), by (name_pattern: 'RES_0402', value_pattern: '10K 0402 1%'), comment: 'Use 50V by default'
│       └── manufacturer: 'UNI-ROYAL(Uniroyal Elec)', mpn: '0402WGF1002TCE' (Auto-selected)
├── R409 (name: 'RES_0402', value: '10K 0402 1%')
│   └── Substituted (name: 'RES_0402', value: '10K 0402 1% 50V'), by (name_pattern: 'RES_0402', value_pattern: '10K 0402 1%'), comment: 'Use 50V by default'
│       └── manufacturer: 'UNI-ROYAL(Uniroyal Elec)', mpn: '0402WGF1002TCE' (Auto-selected)
├── R601 (name: 'RES_0402', value: '5K1 0402 1%')
│   └── Substituted (name: 'RES_0402', value: '5K1 0402 1% 50V'), by (name_pattern: 'RES_0402', value_pattern: '5K1 0402 1%'), comment: 'Use 50V by default'
│       └── manufacturer: 'UNI-ROYAL(Uniroyal Elec)', mpn: '0402WGF5101TCE' (Auto-selected)
├── R602 (name: 'RES_0402', value: '5K1 0402 1%')
│   └── Substituted (name: 'RES_0402', value: '5K1 0402 1% 50V'), by (name_pattern: 'RES_0402', value_pattern: '5K1 0402 1%'), comment: 'Use 50V by default'
│       └── manufacturer: 'UNI-ROYAL(Uniroyal Elec)', mpn: '0402WGF5101TCE' (Auto-selected)
├── R603 (name: 'RES_0402', value: '5K1 0402 1%')
│   └── Substituted (name: 'RES_0402', value: '5K1 0402 1% 50V'), by (name_pattern: 'RES_0402', value_pattern: '5K1 0402 1%'), comment: 'Use 50V by default'
│       └── manufacturer: 'UNI-ROYAL(Uniroyal Elec)', mpn: '0402WGF5101TCE' (Auto-selected)
├── R604 (name: 'RES_0402', value: '5K1 0402 1%')
│   └── Substituted (name: 'RES_0402', value: '5K1 0402 1% 50V'), by (name_pattern: 'RES_0402', value_pattern: '5K1 0402 1%'), comment: 'Use 50V by default'
│       └── manufacturer: 'UNI-ROYAL(Uniroyal Elec)', mpn: '0402WGF5101TCE' (Auto-selected)
├── R605 (name: 'RES_0402', value: '10K 0402 1%')
│   └── Substituted (name: 'RES_0402', value: '10K 0402 1% 50V'), by (name_pattern: 'RES_0402', value_pattern: '10K 0402 1%'), comment: 'Use 50V by default'
│       └── manufacturer: 'UNI-ROYAL(Uniroyal Elec)', mpn: '0402WGF1002TCE' (Auto-selected)
├── R606 (name: 'RES_0402', value: '10K 0402 1%')
│   └── Substituted (name: 'RES_0402', value: '10K 0402 1% 50V'), by (name_pattern: 'RES_0402', value_pattern: '10K 0402 1%'), comment: 'Use 50V by default'
│       └── manufacturer: 'UNI-ROYAL(Uniroyal Elec)', mpn: '0402WGF1002TCE' (Auto-selected)
├── R607 (name: 'RES_0402', value: '4K7 0402 1%')
│   └── Substituted (name: 'RES_0402', value: '4K7 0402 1% 50V'), by (name_pattern: 'RES_0402', value_pattern: '4K7 0402 1%'), comment: 'Use 50V by default'
│       └── manufacturer: 'UNI-ROYAL(Uniroyal Elec)', mpn: '0402WGF4701TCE' (Auto-selected)
├── R608 (name: 'RES_0402', value: '10K 0402 1%')
│   └── Substituted (name: 'RES_0402', value: '10K 0402 1% 50V'), by (name_pattern: 'RES_0402', value_pattern: '10K 0402 1%'), comment: 'Use 50V by default'
│       └── manufacturer: 'UNI-ROYAL(Uniroyal Elec)', mpn: '0402WGF1002TCE' (Auto-selected)
├── R609 (name: 'RES_0402', value: '4K7 0402 1%')
│   └── Substituted (name: 'RES_0402', value: '4K7 0402 1% 50V'), by (name_pattern: 'RES_0402', value_pattern: '4K7 0402 1%'), comment: 'Use 50V by default'
│       └── manufacturer: 'UNI-ROYAL(Uniroyal Elec)', mpn: '0402WGF4701TCE' (Auto-selected)
├── R610 (name: 'RES_0402', value: '10K 0402 1%')
│   └── Substituted (name: 'RES_0402', value: '10K 0402 1% 50V'), by (name_pattern: 'RES_0402', value_pattern: '10K 0402 1%'), comment: 'Use 50V by default'
│       └── manufacturer: 'UNI-ROYAL(Uniroyal Elec)', mpn: '0402WGF1002TCE' (Auto-selected)
├── R611 (name: 'RES_0402', value: '330R 0402 1%')
│   └── Substituted (name: 'RES_0402', value: '330R 0402 1% 50V'), by (name_pattern: 'RES_0402', value_pattern: '330R 0402 1%'), comment: 'Use 50V by default'
│       └── manufacturer: 'UNI-ROYAL(Uniroyal Elec)', mpn: '0402WGF3300TCE' (Auto-selected)
├── R612 (name: 'RES_0402', value: '330R 0402 1%')
│   └── Substituted (name: 'RES_0402', value: '330R 0402 1% 50V'), by (name_pattern: 'RES_0402', value_pattern: '330R 0402 1%'), comment: 'Use 50V by default'
│       └── manufacturer: 'UNI-ROYAL(Uniroyal Elec)', mpn: '0402WGF3300TCE' (Auto-selected)
├── S401 (name: 'TL1015', value: 'H7_BOOT')
│   └── Substituted (name: 'GT-TC031A-H020-L1N', value: ''), by (name_pattern: 'TL1015', value_pattern: '.*'), comment: 'Use g-switch brand instead'
│       └── manufacturer: 'G-Switch', mpn: 'GT-TC031A-H020-L1N' (Auto-selected)
├── S402 (name: 'TL1015', value: 'ESP_BOOT')
│   └── Substituted (name: 'GT-TC031A-H020-L1N', value: ''), by (name_pattern: 'TL1015', value_pattern: '.*'), comment: 'Use g-switch brand instead'
│       └── manufacturer: 'G-Switch', mpn: 'GT-TC031A-H020-L1N' (Auto-selected)
├── S403 (name: 'TL1015', value: '')
│   └── Substituted (name: 'GT-TC031A-H020-L1N', value: ''), by (name_pattern: 'TL1015', value_pattern: '.*'), comment: 'Use g-switch brand instead'
│       └── manufacturer: 'G-Switch', mpn: 'GT-TC031A-H020-L1N' (Auto-selected)
├── S404 (name: 'TL1015', value: '')
│   └── Substituted (name: 'GT-TC031A-H020-L1N', value: ''), by (name_pattern: 'TL1015', value_pattern: '.*'), comment: 'Use g-switch brand instead'
│       └── manufacturer: 'G-Switch', mpn: 'GT-TC031A-H020-L1N' (Auto-selected)
├── S405 (name: 'TL1015', value: 'ESP_BOOT')
│   └── Substituted (name: 'GT-TC031A-H020-L1N', value: ''), by (name_pattern: 'TL1015', value_pattern: '.*'), comment: 'Use g-switch brand instead'
│       └── manufacturer: 'G-Switch', mpn: 'GT-TC031A-H020-L1N' (Auto-selected)
├── S406 (name: 'TL1015', value: 'ESP_BOOT')
│   └── Substituted (name: 'GT-TC031A-H020-L1N', value: ''), by (name_pattern: 'TL1015', value_pattern: '.*'), comment: 'Use g-switch brand instead'
│       └── manufacturer: 'G-Switch', mpn: 'GT-TC031A-H020-L1N' (Auto-selected)
├── U1 (name: 'TPS3820-50DBVx', value: '')
│   └── manufacturer: 'Texas Instruments', mpn: 'TPS3820-50DBVR' (Auto-selected)
├── U2 (name: 'TPS62A02PDDCR', value: '')
│   └── manufacturer: 'Texas Instruments', mpn: 'TPS62A02PDDCR' (Auto-selected)
├── U3 (name: 'TPS62A02PDDCR', value: '')
│   └── manufacturer: 'Texas Instruments', mpn: 'TPS62A02PDDCR' (Auto-selected)
├── U4 (name: 'TPS62A02PDDCR', value: '')
│   └── manufacturer: 'Texas Instruments', mpn: 'TPS62A02PDDCR' (Auto-selected)
├── U101 (name: 'STM32H725IxK_SPLIT', value: '')
│   └── Substituted (name: 'STM32H725IxK', value: ''), by (name_pattern: 'STM32H725IxK_SPLIT', value_pattern: ''), comment: 'Use non-split-component for lookups'
│       └── Substituted (name: 'STM32H725IxK', value: 'STM32H725IGK6'), by (name_pattern: 'STM32H725IxK', value_pattern: ''), comment: 'Use 'G' version, 1MB ram'
│           └── manufacturer: 'ST', mpn: 'STM32H725IGK6' (Auto-selected)
├── U102 (name: 'ICE40HX8K-CT256', value: '')
│   └── manufacturer: 'Lattice', mpn: 'ICE40HX8K-CT256' (Auto-selected)
├── U103 (name: 'W25Q16JVUXIQ/W25Q16JVUXIM', value: '')
│   └── Substituted (name: 'W25Q16JVUXIQ', value: ''), by (name_pattern: 'W25Q16JVUXIQ/W25Q16JVUXIM', value_pattern: ''), comment: ''
│       └── manufacturer: 'WINBOND', mpn: 'W25Q16JVUXIQ' (Auto-selected)
├── U104 (name: 'ESP32-C6-MINI-1-H4_SPLIT', value: '')
│   └── Substituted (name: 'ESP32-C6-MINI-1-H4', value: ''), by (name_pattern: 'ESP32-C6-MINI-1-H4_SPLIT', value_pattern: ''), comment: 'Use non-split-component for lookups'
│       └── manufacturer: 'Espressif Systems', mpn: 'ESP32-C3-MINI-1-H4' (Auto-selected)
├── U301 (name: 'SN3257QDYYRQ1', value: '')
│   └── manufacturer: 'Texas Instruments', mpn: 'SN3257QDYYRQ1' (Auto-selected)
├── U302 (name: 'SN3257QDYYRQ1', value: '')
│   └── manufacturer: 'Texas Instruments', mpn: 'SN3257QDYYRQ1' (Auto-selected)
├── U303 (name: 'SN3257QDYYRQ1', value: '')
│   └── manufacturer: 'Texas Instruments', mpn: 'SN3257QDYYRQ1' (Auto-selected)
├── U304 (name: 'SN3257QDYYRQ1', value: '')
│   └── manufacturer: 'Texas Instruments', mpn: 'SN3257QDYYRQ1' (Auto-selected)
├── U601 (name: 'TMUXHS221NKGR', value: '')
│   └── manufacturer: 'Texas Instruments', mpn: 'TMUXHS221NKGR' (Auto-selected)
├── U602 (name: 'TMUXHS221NKGR', value: '')
│   └── manufacturer: 'Texas Instruments', mpn: 'TMUXHS221NKGR' (Auto-selected)
└── Y101 (name: '8132H-50.000ML33DTL', value: '50Mhz HCMOS output')
    └── manufacturer: 'HCI', mpn: '8132H-50.000ML33DTL' (Auto-selected)

variantbuilder_app: All placements mapped!
variantbuilder_app: Output written to 'MakerPnPControl-core_variant1_placements.csv'
variantbuilder_app: BOM written to 'MakerPnPControl-core_variant1_bom.csv'

Process finished with exit code 0

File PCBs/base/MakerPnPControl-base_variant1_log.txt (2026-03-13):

D:\Users\Hydra\Documents\dev\projects\makerpnp\makerpnp\target\release\variantbuilder_cli.exe @MakerPnPControl_variant1.args
stores::eda_placements: Loading eda placements. source: Export/MakerPnPControl-PCB/MakerPnPControl-PnP.csv
variantbuilder_app: Loaded 454 placements
variantbuilder_app: excluding placements: ["C35", "C36", "C37", "C38", "C39", "MH1_PE", "MH1", "MH2", "MH3", "MH4"]
stores::substitutions: Loading eda substitutions. source: MakerPnPControl_variant1_substitutions.csv
variantbuilder_app: Loaded 9 substitution rules from MakerPnPControl_variant1_substitutions.csv
stores::substitutions: Loading eda substitutions. source: global-substitutions.csv
variantbuilder_app: Loaded 108 substitution rules from global-substitutions.csv
variantbuilder_app: disabling placements: []
stores::parts: Loading parts. source: parts.csv
variantbuilder_app: Loaded 165 parts
stores::part_mappings: Loading part mappings. source: part-mappings.csv
variantbuilder_app: Loaded 160 part mappings
variantbuilder_app: Loaded 0 load-out items
stores::assembly_rules: Loading assembly rules. source: MakerPnPControl_variant1_rules.csv
variantbuilder_app: Loaded 2 assembly rules
variantbuilder_app: Assembly variant: Default
variantbuilder_app: Ref_des list:
variantbuilder_app: Matched 444 placements for assembly variant
variantbuilder_app: Mapping Result
├── C1 (name: 'UMK325B7475MMHT', value: '4.7uF 50V 1210 X7R 20%')
│   └── Substituted (name: 'CAP_1210_N', value: '4.7uF 50V 1210 X7R 10%'), by (name_pattern: 'UMK325B7475MMHT', value_pattern: '4.7uF 50V 1210 X7R 20%'), de-rate: 'from 20% to 10%'
│       └── manufacturer: 'Samsung Electro-Mechanics', mpn: 'CL32B475KBUYNNE' (Auto-selected)
├── C2 (name: 'UMK325B7475MMHT', value: '4.7uF 50V 1210 X7R 20%')
│   └── Substituted (name: 'CAP_1210_N', value: '4.7uF 50V 1210 X7R 10%'), by (name_pattern: 'UMK325B7475MMHT', value_pattern: '4.7uF 50V 1210 X7R 20%'), de-rate: 'from 20% to 10%'
│       └── manufacturer: 'Samsung Electro-Mechanics', mpn: 'CL32B475KBUYNNE' (Auto-selected)
├── C3 (name: 'UMK325B7475MMHT', value: '4.7uF 50V 1210 X7R 20%')
│   └── Substituted (name: 'CAP_1210_N', value: '4.7uF 50V 1210 X7R 10%'), by (name_pattern: 'UMK325B7475MMHT', value_pattern: '4.7uF 50V 1210 X7R 20%'), de-rate: 'from 20% to 10%'
│       └── manufacturer: 'Samsung Electro-Mechanics', mpn: 'CL32B475KBUYNNE' (Auto-selected)
├── C4 (name: 'GRM155R71H223KA12D', value: '22nF 50V 0402 X7R 20%')
│   └── manufacturer: 'Murata Electronics', mpn: 'GRM155R71H223KA12D' (Auto-selected)
├── C5 (name: 'GRM155R71H223KA12D', value: '22nF 50V 0402 X7R 20%')
│   └── manufacturer: 'Murata Electronics', mpn: 'GRM155R71H223KA12D' (Auto-selected)
├── C6 (name: 'CAP_0603_N', value: '100nF 63V 0603 X5R 10%')
│   └── Substituted (name: 'CAP_0603_N', value: '100nF 100V 0603 X7R 10%'), by (name_pattern: 'CAP_0603_N', value_pattern: '100nF 63V 0603 X5R 10%'), de-rate: 'from 63V to 100V', de-rate: 'from X5R to X7R'
│       └── manufacturer: 'Samsung Electro-Mechanics', mpn: 'CL10B104KC8NNNC' (Auto-selected)
├── C7 (name: 'UMK325B7475MMHT', value: '4.7uF 50V 1210 X7R 20%')
│   └── Substituted (name: 'CAP_1210_N', value: '4.7uF 50V 1210 X7R 10%'), by (name_pattern: 'UMK325B7475MMHT', value_pattern: '4.7uF 50V 1210 X7R 20%'), de-rate: 'from 20% to 10%'
│       └── manufacturer: 'Samsung Electro-Mechanics', mpn: 'CL32B475KBUYNNE' (Auto-selected)
├── C8 (name: 'UMK325B7475MMHT', value: '4.7uF 50V 1210 X7R 20%')
│   └── Substituted (name: 'CAP_1210_N', value: '4.7uF 50V 1210 X7R 10%'), by (name_pattern: 'UMK325B7475MMHT', value_pattern: '4.7uF 50V 1210 X7R 20%'), de-rate: 'from 20% to 10%'
│       └── manufacturer: 'Samsung Electro-Mechanics', mpn: 'CL32B475KBUYNNE' (Auto-selected)
├── C9 (name: 'GRM155R71H223KA12D', value: '22nF 50V 0402 X7R 20%')
│   └── manufacturer: 'Murata Electronics', mpn: 'GRM155R71H223KA12D' (Auto-selected)
├── C10 (name: 'GRM155R71H223KA12D', value: '22nF 50V 0402 X7R 20%')
│   └── manufacturer: 'Murata Electronics', mpn: 'GRM155R71H223KA12D' (Auto-selected)
├── C11 (name: 'CAP_0603_N', value: '1uF 16V 0603 X7R')
│   └── Substituted (name: 'CAP_0603_N', value: '1uF 25V 0603 X7R 10%'), by (name_pattern: 'CAP_0603_N', value_pattern: '1uF 16V 0603 X7R'), de-rate: 'from 16V to 25V', comment: 'Use 10% by default'
│       └── manufacturer: 'Samsung Electro-Mechanics', mpn: 'CL10B105KA8NNNC' (Auto-selected)
├── C12 (name: 'CAP_0603_N', value: '1uF 16V 0603 X7R')
│   └── Substituted (name: 'CAP_0603_N', value: '1uF 25V 0603 X7R 10%'), by (name_pattern: 'CAP_0603_N', value_pattern: '1uF 16V 0603 X7R'), de-rate: 'from 16V to 25V', comment: 'Use 10% by default'
│       └── manufacturer: 'Samsung Electro-Mechanics', mpn: 'CL10B105KA8NNNC' (Auto-selected)
├── C13 (name: 'CAP_0805_N', value: '22uF 25V 0805 X5R')
│   └── Substituted (name: 'CAP_0805_N', value: '22uF 25V 0805 X5R 20%'), by (name_pattern: 'CAP_0805_N', value_pattern: '22uF 25V 0805 X5R'), comment: 'Use 20% by default'
│       └── manufacturer: 'Samsung Electro-Mechanics', mpn: 'CL10B104KB8NNNC' (Auto-selected)
├── C14 (name: 'CAP_0805_N', value: '22uF 25V 0805 X5R')
│   └── Substituted (name: 'CAP_0805_N', value: '22uF 25V 0805 X5R 20%'), by (name_pattern: 'CAP_0805_N', value_pattern: '22uF 25V 0805 X5R'), comment: 'Use 20% by default'
│       └── manufacturer: 'Samsung Electro-Mechanics', mpn: 'CL10B104KB8NNNC' (Auto-selected)
├── C15 (name: 'CAP_0603_N', value: '100nF 63V 0603 X5R 10%')
│   └── Substituted (name: 'CAP_0603_N', value: '100nF 100V 0603 X7R 10%'), by (name_pattern: 'CAP_0603_N', value_pattern: '100nF 63V 0603 X5R 10%'), de-rate: 'from 63V to 100V', de-rate: 'from X5R to X7R'
│       └── manufacturer: 'Samsung Electro-Mechanics', mpn: 'CL10B104KC8NNNC' (Auto-selected)
├── C16 (name: 'CAP_0603_N', value: '100nF 63V 0603 X5R 10%')
│   └── Substituted (name: 'CAP_0603_N', value: '100nF 100V 0603 X7R 10%'), by (name_pattern: 'CAP_0603_N', value_pattern: '100nF 63V 0603 X5R 10%'), de-rate: 'from 63V to 100V', de-rate: 'from X5R to X7R'
│       └── manufacturer: 'Samsung Electro-Mechanics', mpn: 'CL10B104KC8NNNC' (Auto-selected)
├── C17 (name: 'CAP_0603_N', value: '22pF 16V 0603 C0G 5%')
│   └── manufacturer: 'Samsung Electro-Mechanics', mpn: 'CL10C220JB8NNNC' (Auto-selected)
├── C18 (name: 'CAP_0603_N', value: '22pF 16V 0603 C0G 5%')
│   └── manufacturer: 'Samsung Electro-Mechanics', mpn: 'CL10C220JB8NNNC' (Auto-selected)
├── C19 (name: 'CAP_0603_N', value: '10uF 16V 0603 X5R 20%')
│   └── manufacturer: 'Samsung Electro-Mechanics', mpn: 'CL10A106MA8NRNC' (Auto-selected)
├── C20 (name: 'CAP_0603_N', value: '100nF 16V 0603 X7R 10%')
│   └── Substituted (name: 'CAP_0603_N', value: '100nF 100V 0603 X7R 10%'), by (name_pattern: 'CAP_0603_N', value_pattern: '100nF 16V 0603 X7R 10%'), de-rate: 'from 16V to 100V'
│       └── manufacturer: 'Samsung Electro-Mechanics', mpn: 'CL10B104KC8NNNC' (Auto-selected)
├── C21 (name: 'CAP_1210', value: '47uF 16V 1210 X7R')
│   └── Substituted (name: 'CAP_1210', value: '47uF 16V 1210 X7R 10%'), by (name_pattern: 'CAP_1210', value_pattern: '47uF 16V 1210 X7R'), comment: 'Use 10% by default'
│       └── manufacturer: 'Samwha Capacitor', mpn: 'CS3225X7R476K160NRL' (Auto-selected)
├── C22 (name: 'CAP_1210', value: '47uF 16V 1210 X7R')
│   └── Substituted (name: 'CAP_1210', value: '47uF 16V 1210 X7R 10%'), by (name_pattern: 'CAP_1210', value_pattern: '47uF 16V 1210 X7R'), comment: 'Use 10% by default'
│       └── manufacturer: 'Samwha Capacitor', mpn: 'CS3225X7R476K160NRL' (Auto-selected)
├── C23 (name: 'CAP_1210', value: '47uF 16V 1210 X7R')
│   └── Substituted (name: 'CAP_1210', value: '47uF 16V 1210 X7R 10%'), by (name_pattern: 'CAP_1210', value_pattern: '47uF 16V 1210 X7R'), comment: 'Use 10% by default'
│       └── manufacturer: 'Samwha Capacitor', mpn: 'CS3225X7R476K160NRL' (Auto-selected)
├── C24 (name: 'CAP_1210', value: '47uF 16V 1210 X7R')
│   └── Substituted (name: 'CAP_1210', value: '47uF 16V 1210 X7R 10%'), by (name_pattern: 'CAP_1210', value_pattern: '47uF 16V 1210 X7R'), comment: 'Use 10% by default'
│       └── manufacturer: 'Samwha Capacitor', mpn: 'CS3225X7R476K160NRL' (Auto-selected)
├── C25 (name: 'CAP_1210', value: '47uF 16V 1210 X7R')
│   └── Substituted (name: 'CAP_1210', value: '47uF 16V 1210 X7R 10%'), by (name_pattern: 'CAP_1210', value_pattern: '47uF 16V 1210 X7R'), comment: 'Use 10% by default'
│       └── manufacturer: 'Samwha Capacitor', mpn: 'CS3225X7R476K160NRL' (Auto-selected)
├── C26 (name: 'CAP_1210', value: '47uF 16V 1210 X7R')
│   └── Substituted (name: 'CAP_1210', value: '47uF 16V 1210 X7R 10%'), by (name_pattern: 'CAP_1210', value_pattern: '47uF 16V 1210 X7R'), comment: 'Use 10% by default'
│       └── manufacturer: 'Samwha Capacitor', mpn: 'CS3225X7R476K160NRL' (Auto-selected)
├── C27 (name: 'CAPP_1206_N', value: '22uF 16V 1206 TANTALUM 20%')
│   └── manufacturer: 'KYOCERA AVX', mpn: 'TAJA226M016RNJ' (Auto-selected)
├── C28 (name: 'CAP_1210', value: '47uF 16V 1210 X7R')
│   └── Substituted (name: 'CAP_1210', value: '47uF 16V 1210 X7R 10%'), by (name_pattern: 'CAP_1210', value_pattern: '47uF 16V 1210 X7R'), comment: 'Use 10% by default'
│       └── manufacturer: 'Samwha Capacitor', mpn: 'CS3225X7R476K160NRL' (Auto-selected)
├── C29 (name: 'CAP_1210', value: '47uF 16V 1210 X7R')
│   └── Substituted (name: 'CAP_1210', value: '47uF 16V 1210 X7R 10%'), by (name_pattern: 'CAP_1210', value_pattern: '47uF 16V 1210 X7R'), comment: 'Use 10% by default'
│       └── manufacturer: 'Samwha Capacitor', mpn: 'CS3225X7R476K160NRL' (Auto-selected)
├── C30 (name: 'VKME1651J331MV', value: '330uF 63V 20%')
│   └── manufacturer: 'Ymin', mpn: 'VKME1651J331MV' (Auto-selected)
├── C31 (name: 'VKME1651J331MV', value: '330uF 63V 20%')
│   └── manufacturer: 'Ymin', mpn: 'VKME1651J331MV' (Auto-selected)
├── C32 (name: 'VKME1651J331MV', value: '330uF 63V 20%')
│   └── manufacturer: 'Ymin', mpn: 'VKME1651J331MV' (Auto-selected)
├── C33 (name: 'VKME1651J331MV', value: '330uF 63V 20%')
│   └── manufacturer: 'Ymin', mpn: 'VKME1651J331MV' (Auto-selected)
├── C34 (name: 'CAP_0402', value: '100nF 6.3V 0402')
│   └── Substituted (name: 'CAP_0402', value: '100nF 6.3V 0402 X7R 10%'), by (name_pattern: 'CAP_0402', value_pattern: '100nF 6.3V 0402'), comment: 'Use X7R 10% by default'
│       └── Substituted (name: 'CAP_0402', value: '100nF 16V 0402 X7R 10%'), by (name_pattern: 'CAP_0402', value_pattern: '100nF 6.3V 0402 X7R 10%'), de-rate: 'from 6.3V to 16V'
│           └── Substituted (name: 'CAP_0402', value: '100nF 25V 0402 X7R 10%'), by (name_pattern: 'CAP_0402', value_pattern: '100nF 16V 0402 X7R 10%'), de-rate: 'from 16V to 25V', comment: 'BOM consolidation'
│               └── manufacturer: 'Samsung Electro-Mechanics', mpn: 'CL05B104KA5NNNC' (Auto-selected)
├── C40 (name: 'CAP_1812_N', value: '4.7nF 2kV 1812')
│   └── manufacturer: 'Walsin Tech Corp', mpn: '1812B472K202CT' (Auto-selected)
├── C41 (name: 'UMK325B7475MMHT', value: '4.7uF 50V 1210 X7R 20%')
│   └── Substituted (name: 'CAP_1210_N', value: '4.7uF 50V 1210 X7R 10%'), by (name_pattern: 'UMK325B7475MMHT', value_pattern: '4.7uF 50V 1210 X7R 20%'), de-rate: 'from 20% to 10%'
│       └── manufacturer: 'Samsung Electro-Mechanics', mpn: 'CL32B475KBUYNNE' (Auto-selected)
├── C42 (name: 'UMK325B7475MMHT', value: '4.7uF 50V 1210 X7R 20%')
│   └── Substituted (name: 'CAP_1210_N', value: '4.7uF 50V 1210 X7R 10%'), by (name_pattern: 'UMK325B7475MMHT', value_pattern: '4.7uF 50V 1210 X7R 20%'), de-rate: 'from 20% to 10%'
│       └── manufacturer: 'Samsung Electro-Mechanics', mpn: 'CL32B475KBUYNNE' (Auto-selected)
├── C43 (name: 'CAP_0603_N', value: '100nF 63V 0603 X5R 10%')
│   └── Substituted (name: 'CAP_0603_N', value: '100nF 100V 0603 X7R 10%'), by (name_pattern: 'CAP_0603_N', value_pattern: '100nF 63V 0603 X5R 10%'), de-rate: 'from 63V to 100V', de-rate: 'from X5R to X7R'
│       └── manufacturer: 'Samsung Electro-Mechanics', mpn: 'CL10B104KC8NNNC' (Auto-selected)
├── C44 (name: 'CAP_0603_N', value: '100nF 63V 0603 X5R 10%')
│   └── Substituted (name: 'CAP_0603_N', value: '100nF 100V 0603 X7R 10%'), by (name_pattern: 'CAP_0603_N', value_pattern: '100nF 63V 0603 X5R 10%'), de-rate: 'from 63V to 100V', de-rate: 'from X5R to X7R'
│       └── manufacturer: 'Samsung Electro-Mechanics', mpn: 'CL10B104KC8NNNC' (Auto-selected)
├── C45 (name: 'CAP_0805_N', value: '22uF 25V 0805 X5R')
│   └── Substituted (name: 'CAP_0805_N', value: '22uF 25V 0805 X5R 20%'), by (name_pattern: 'CAP_0805_N', value_pattern: '22uF 25V 0805 X5R'), comment: 'Use 20% by default'
│       └── manufacturer: 'Samsung Electro-Mechanics', mpn: 'CL10B104KB8NNNC' (Auto-selected)
├── C46 (name: 'CAP_0805_N', value: '22uF 25V 0805 X5R')
│   └── Substituted (name: 'CAP_0805_N', value: '22uF 25V 0805 X5R 20%'), by (name_pattern: 'CAP_0805_N', value_pattern: '22uF 25V 0805 X5R'), comment: 'Use 20% by default'
│       └── manufacturer: 'Samsung Electro-Mechanics', mpn: 'CL10B104KB8NNNC' (Auto-selected)
├── C47 (name: 'CAP_0805_N', value: '22uF 25V 0805 X5R')
│   └── Substituted (name: 'CAP_0805_N', value: '22uF 25V 0805 X5R 20%'), by (name_pattern: 'CAP_0805_N', value_pattern: '22uF 25V 0805 X5R'), comment: 'Use 20% by default'
│       └── manufacturer: 'Samsung Electro-Mechanics', mpn: 'CL10B104KB8NNNC' (Auto-selected)
├── C48 (name: 'CAP_0805_N', value: '22uF 25V 0805 X5R')
│   └── Substituted (name: 'CAP_0805_N', value: '22uF 25V 0805 X5R 20%'), by (name_pattern: 'CAP_0805_N', value_pattern: '22uF 25V 0805 X5R'), comment: 'Use 20% by default'
│       └── manufacturer: 'Samsung Electro-Mechanics', mpn: 'CL10B104KB8NNNC' (Auto-selected)
├── C49 (name: 'CAP_0603_N', value: '100nF 16V 0603 X7R 10%')
│   └── Substituted (name: 'CAP_0603_N', value: '100nF 100V 0603 X7R 10%'), by (name_pattern: 'CAP_0603_N', value_pattern: '100nF 16V 0603 X7R 10%'), de-rate: 'from 16V to 100V'
│       └── manufacturer: 'Samsung Electro-Mechanics', mpn: 'CL10B104KC8NNNC' (Auto-selected)
├── C50 (name: 'CAP_0603_N', value: '100nF 16V 0603 X7R 10%')
│   └── Substituted (name: 'CAP_0603_N', value: '100nF 100V 0603 X7R 10%'), by (name_pattern: 'CAP_0603_N', value_pattern: '100nF 16V 0603 X7R 10%'), de-rate: 'from 16V to 100V'
│       └── manufacturer: 'Samsung Electro-Mechanics', mpn: 'CL10B104KC8NNNC' (Auto-selected)
├── C51 (name: 'CAP_1206_N', value: '10uF 16V 1206 X7R')
│   └── Substituted (name: 'CAP_1206_N', value: '10uF 25V 1206 X7R 10%'), by (name_pattern: 'CAP_1206_N', value_pattern: '10uF 16V 1206 X7R'), de-rate: 'from 16V to 25V', comment: 'Use 10% by default'
│       └── manufacturer: 'Samsung Electro-Mechanics', mpn: 'CL31B106KAHNNNE' (Auto-selected)
├── C52 (name: 'CAP_1206_N', value: '10uF 16V 1206 X7R')
│   └── Substituted (name: 'CAP_1206_N', value: '10uF 25V 1206 X7R 10%'), by (name_pattern: 'CAP_1206_N', value_pattern: '10uF 16V 1206 X7R'), de-rate: 'from 16V to 25V', comment: 'Use 10% by default'
│       └── manufacturer: 'Samsung Electro-Mechanics', mpn: 'CL31B106KAHNNNE' (Auto-selected)
├── C53 (name: 'CAP_0603_N', value: '100nF 16V 0603 X7R 10%')
│   └── Substituted (name: 'CAP_0603_N', value: '100nF 100V 0603 X7R 10%'), by (name_pattern: 'CAP_0603_N', value_pattern: '100nF 16V 0603 X7R 10%'), de-rate: 'from 16V to 100V'
│       └── manufacturer: 'Samsung Electro-Mechanics', mpn: 'CL10B104KC8NNNC' (Auto-selected)
├── C54 (name: 'CAP_0603_N', value: '100nF 16V 0603 X7R 10%')
│   └── Substituted (name: 'CAP_0603_N', value: '100nF 100V 0603 X7R 10%'), by (name_pattern: 'CAP_0603_N', value_pattern: '100nF 16V 0603 X7R 10%'), de-rate: 'from 16V to 100V'
│       └── manufacturer: 'Samsung Electro-Mechanics', mpn: 'CL10B104KC8NNNC' (Auto-selected)
├── C55 (name: 'CAP_0603_N', value: '100nF 16V 0603 X7R 10%')
│   └── Substituted (name: 'CAP_0603_N', value: '100nF 100V 0603 X7R 10%'), by (name_pattern: 'CAP_0603_N', value_pattern: '100nF 16V 0603 X7R 10%'), de-rate: 'from 16V to 100V'
│       └── manufacturer: 'Samsung Electro-Mechanics', mpn: 'CL10B104KC8NNNC' (Auto-selected)
├── C56 (name: 'CAP_0603_N', value: '100nF 16V 0603 X7R 10%')
│   └── Substituted (name: 'CAP_0603_N', value: '100nF 100V 0603 X7R 10%'), by (name_pattern: 'CAP_0603_N', value_pattern: '100nF 16V 0603 X7R 10%'), de-rate: 'from 16V to 100V'
│       └── manufacturer: 'Samsung Electro-Mechanics', mpn: 'CL10B104KC8NNNC' (Auto-selected)
├── C57 (name: 'CAP_0402', value: '100nF 25V 0402 X5R')
│   └── Substituted (name: 'CAP_0402', value: '100nF 25V 0402 X7R 10%'), by (name_pattern: 'CAP_0402', value_pattern: '100nF 25V 0402 X5R'), de-rate: 'from X5R to X7R', comment: 'Use 10% by default'
│       └── manufacturer: 'Samsung Electro-Mechanics', mpn: 'CL05B104KA5NNNC' (Auto-selected)
├── C58 (name: 'CAP_0402', value: '100nF 25V 0402 X5R')
│   └── Substituted (name: 'CAP_0402', value: '100nF 25V 0402 X7R 10%'), by (name_pattern: 'CAP_0402', value_pattern: '100nF 25V 0402 X5R'), de-rate: 'from X5R to X7R', comment: 'Use 10% by default'
│       └── manufacturer: 'Samsung Electro-Mechanics', mpn: 'CL05B104KA5NNNC' (Auto-selected)
├── C59 (name: 'CAP_0603_N', value: '1uF 25V 0603 X5R')
│   └── Substituted (name: 'CAP_0603_N', value: '1uF 25V 0603 X7R 10%'), by (name_pattern: 'CAP_0603_N', value_pattern: '1uF 25V 0603 X5R'), de-rate: 'from X5R to X7R', comment: 'Use 10% by default'
│       └── manufacturer: 'Samsung Electro-Mechanics', mpn: 'CL10B105KA8NNNC' (Auto-selected)
├── C60 (name: 'CAP_0603_N', value: '1uF 25V 0603 X5R')
│   └── Substituted (name: 'CAP_0603_N', value: '1uF 25V 0603 X7R 10%'), by (name_pattern: 'CAP_0603_N', value_pattern: '1uF 25V 0603 X5R'), de-rate: 'from X5R to X7R', comment: 'Use 10% by default'
│       └── manufacturer: 'Samsung Electro-Mechanics', mpn: 'CL10B105KA8NNNC' (Auto-selected)
├── C61 (name: 'CAP_0603_N', value: '1nF 25V 0603 X5R')
│   └── Substituted (name: 'CAP_0603_N', value: '1nF 50V 0603 X7R 10%'), by (name_pattern: 'CAP_0603_N', value_pattern: '1nF 25V 0603 X5R'), de-rate: 'from 25V to 50V', de-rate: 'from X5R to X7R', comment: 'Use 10% by default'
│       └── manufacturer: 'Samsung Electro-Mechanics', mpn: 'CL10B102KB8NNNC' (Auto-selected)
├── C62 (name: 'CAP_0603_N', value: '1nF 25V 0603 X5R')
│   └── Substituted (name: 'CAP_0603_N', value: '1nF 50V 0603 X7R 10%'), by (name_pattern: 'CAP_0603_N', value_pattern: '1nF 25V 0603 X5R'), de-rate: 'from 25V to 50V', de-rate: 'from X5R to X7R', comment: 'Use 10% by default'
│       └── manufacturer: 'Samsung Electro-Mechanics', mpn: 'CL10B102KB8NNNC' (Auto-selected)
├── C63 (name: 'CAP_0402', value: '100nF 25V 0402 X5R')
│   └── Substituted (name: 'CAP_0402', value: '100nF 25V 0402 X7R 10%'), by (name_pattern: 'CAP_0402', value_pattern: '100nF 25V 0402 X5R'), de-rate: 'from X5R to X7R', comment: 'Use 10% by default'
│       └── manufacturer: 'Samsung Electro-Mechanics', mpn: 'CL05B104KA5NNNC' (Auto-selected)
├── C64 (name: 'CAP_0402', value: '100nF 25V 0402 X5R')
│   └── Substituted (name: 'CAP_0402', value: '100nF 25V 0402 X7R 10%'), by (name_pattern: 'CAP_0402', value_pattern: '100nF 25V 0402 X5R'), de-rate: 'from X5R to X7R', comment: 'Use 10% by default'
│       └── manufacturer: 'Samsung Electro-Mechanics', mpn: 'CL05B104KA5NNNC' (Auto-selected)
├── C65 (name: 'CAP_0603_N', value: '1uF 25V 0603 X5R')
│   └── Substituted (name: 'CAP_0603_N', value: '1uF 25V 0603 X7R 10%'), by (name_pattern: 'CAP_0603_N', value_pattern: '1uF 25V 0603 X5R'), de-rate: 'from X5R to X7R', comment: 'Use 10% by default'
│       └── manufacturer: 'Samsung Electro-Mechanics', mpn: 'CL10B105KA8NNNC' (Auto-selected)
├── C66 (name: 'CAP_0603_N', value: '1uF 25V 0603 X5R')
│   └── Substituted (name: 'CAP_0603_N', value: '1uF 25V 0603 X7R 10%'), by (name_pattern: 'CAP_0603_N', value_pattern: '1uF 25V 0603 X5R'), de-rate: 'from X5R to X7R', comment: 'Use 10% by default'
│       └── manufacturer: 'Samsung Electro-Mechanics', mpn: 'CL10B105KA8NNNC' (Auto-selected)
├── C67 (name: 'CAP_0603_N', value: '1nF 25V 0603 X5R')
│   └── Substituted (name: 'CAP_0603_N', value: '1nF 50V 0603 X7R 10%'), by (name_pattern: 'CAP_0603_N', value_pattern: '1nF 25V 0603 X5R'), de-rate: 'from 25V to 50V', de-rate: 'from X5R to X7R', comment: 'Use 10% by default'
│       └── manufacturer: 'Samsung Electro-Mechanics', mpn: 'CL10B102KB8NNNC' (Auto-selected)
├── C68 (name: 'CAP_0603_N', value: '1nF 25V 0603 X5R')
│   └── Substituted (name: 'CAP_0603_N', value: '1nF 50V 0603 X7R 10%'), by (name_pattern: 'CAP_0603_N', value_pattern: '1nF 25V 0603 X5R'), de-rate: 'from 25V to 50V', de-rate: 'from X5R to X7R', comment: 'Use 10% by default'
│       └── manufacturer: 'Samsung Electro-Mechanics', mpn: 'CL10B102KB8NNNC' (Auto-selected)
├── C69 (name: 'CAP_0603_N', value: '100nF 16V 0603 X7R 10%')
│   └── Substituted (name: 'CAP_0603_N', value: '100nF 100V 0603 X7R 10%'), by (name_pattern: 'CAP_0603_N', value_pattern: '100nF 16V 0603 X7R 10%'), de-rate: 'from 16V to 100V'
│       └── manufacturer: 'Samsung Electro-Mechanics', mpn: 'CL10B104KC8NNNC' (Auto-selected)
├── C70 (name: 'CAP_0603_N', value: '10uF 16V 0603 X5R 20%')
│   └── manufacturer: 'Samsung Electro-Mechanics', mpn: 'CL10A106MA8NRNC' (Auto-selected)
├── C71 (name: 'CAP_0603_N', value: '10uF 16V 0603 X5R 20%')
│   └── manufacturer: 'Samsung Electro-Mechanics', mpn: 'CL10A106MA8NRNC' (Auto-selected)
├── C72 (name: 'CAP_0603_N', value: '10uF 16V 0603 X5R 20%')
│   └── manufacturer: 'Samsung Electro-Mechanics', mpn: 'CL10A106MA8NRNC' (Auto-selected)
├── C73 (name: 'CAP_0402', value: '470pF 6.3V 0402')
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

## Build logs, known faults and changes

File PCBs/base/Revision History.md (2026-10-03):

# Rev A1

## Errata

### issue with U5/U6 ideal diode ORing.

Apparently U6 is the primary, not U5.

The V3P3 rail on the baseboard are thus always supplied by the base board, even when a core board is attached.

No workaround currently.

### Missing pull-up on U18 (SN74HCT245DGSR)

causes outputs to be undefined. observed that the PWM outputs are briefly enabled shortly
after bootup, but are then disabled shortly after.  Timing is undefined.

workaround-1: fit 10k pull-up to OE pin, see hack-1.

workaround-2: (partial) set the GPIO levels as soon as possible on bootup, but this requires running firmware 
so if a CPU is not installed, or a CPU is being firmware upgraded, the outputs will be undefined.

## PM1-4 outputs enabled if V3P3 is missing.

There is a power sequencing and failsafe issue with the PM1-4 outputs.  If the V3P3 rails are not present,
the PM1-4 outputs will be enabled.

The fail-safe output for the ADuM1200 is HIGH when VDDI is missing, this causes the corresponding PM1-4 output
to be enabled.

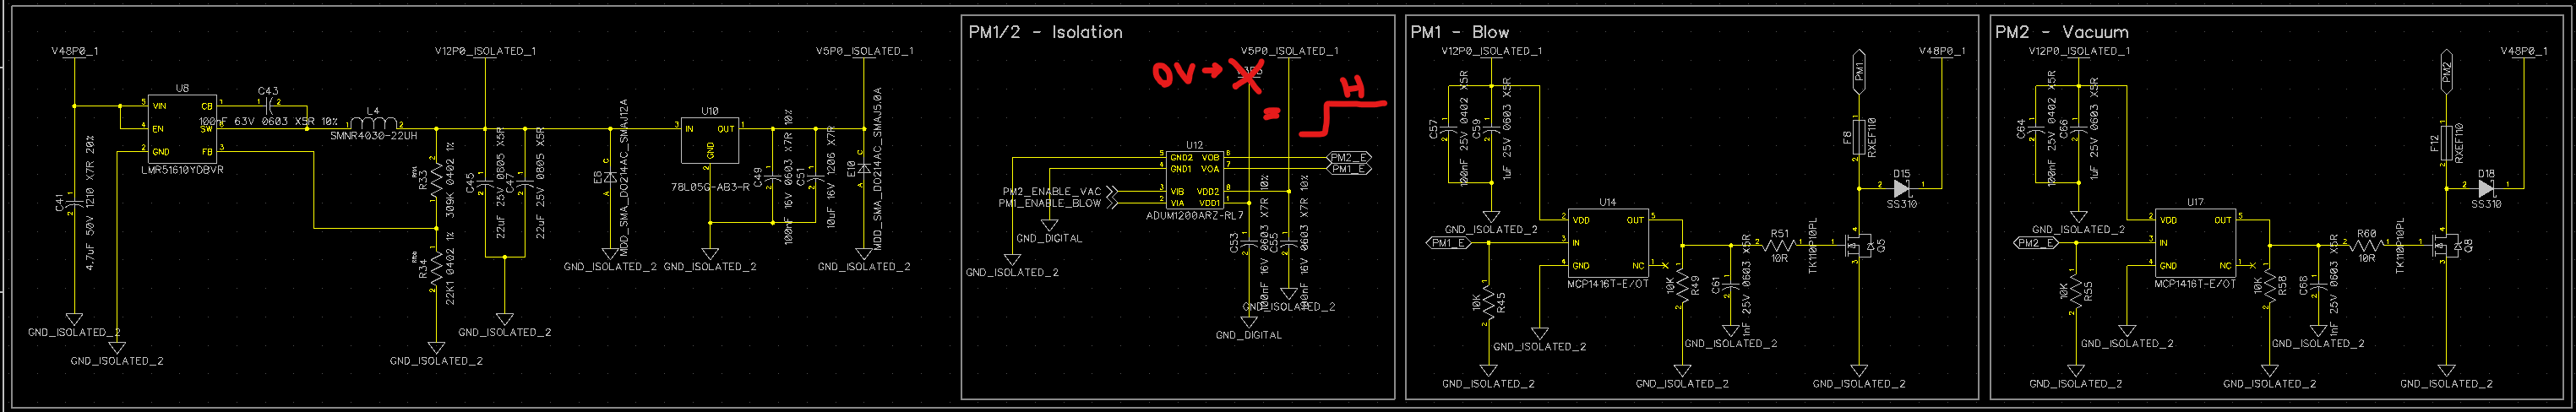
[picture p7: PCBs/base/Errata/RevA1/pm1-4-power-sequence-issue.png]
PM1-4 Power Sequence Issue


workaround-1: replace the ADuM1200 with an ADMuM120N0 or π120M30 which has a LOW fail-safe output, add 10k pull-downs on the PMx_ENABLE
signals.

## Missing VDDIO voltage on ETH

U20:9 was supposed to be connected to VDDIO, but was not.

workaround-1: apply hack 3.

## Hacks

### Hack 1

Missing pull-up on U18 (SN74HCT245DGSR)

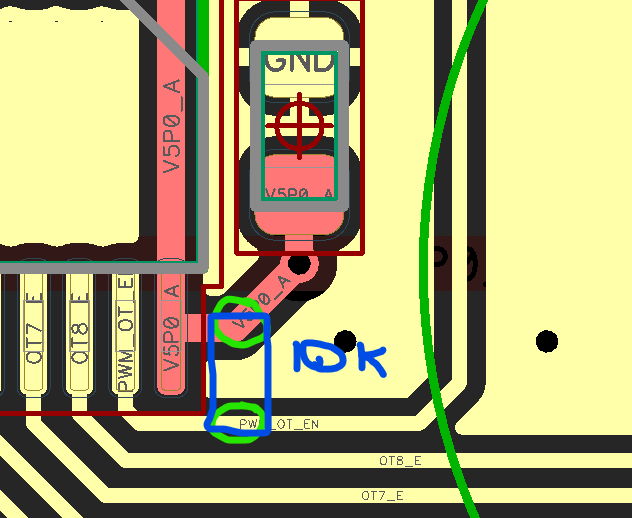
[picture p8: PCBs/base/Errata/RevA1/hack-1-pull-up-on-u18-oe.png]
Hack 1


### Hack 2

Fix PM1-4 fail-safe state.

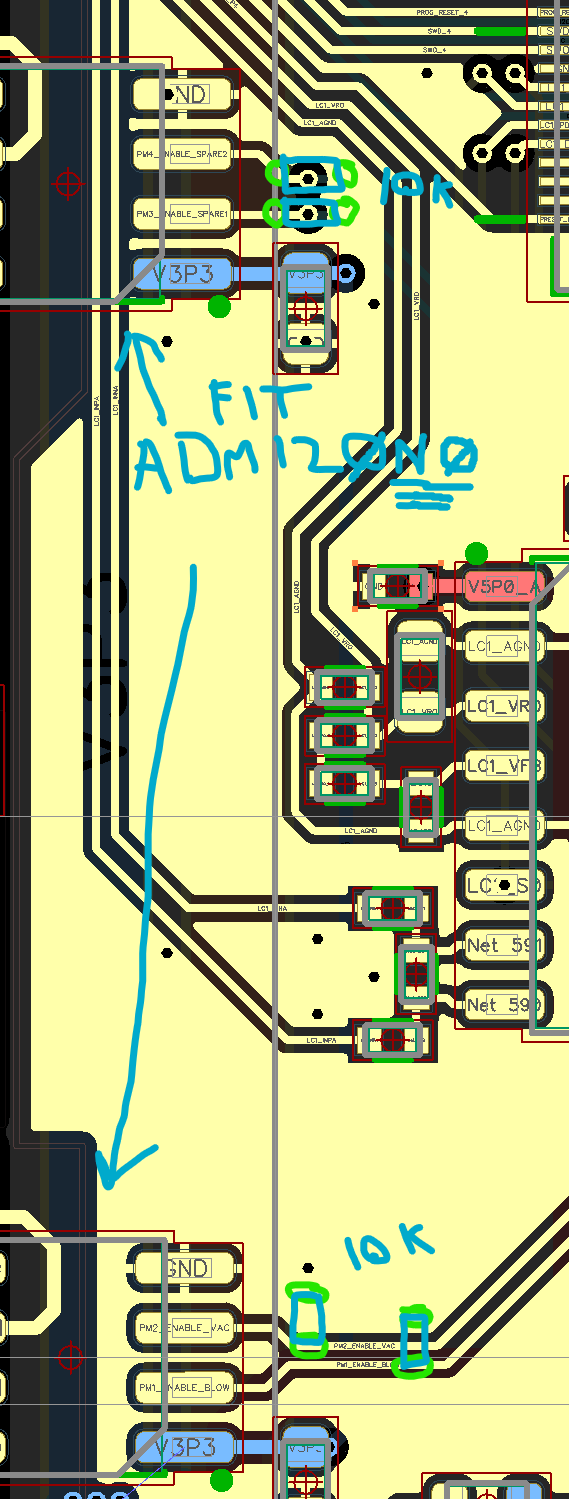
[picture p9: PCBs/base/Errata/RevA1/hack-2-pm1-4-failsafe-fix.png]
Hack 2


### Hack 3

Fix VDDIO on ETH.

Install a 0R resistor or jumper wire between C75:1 and R68:2 *OR* C75:1 and 71:2.

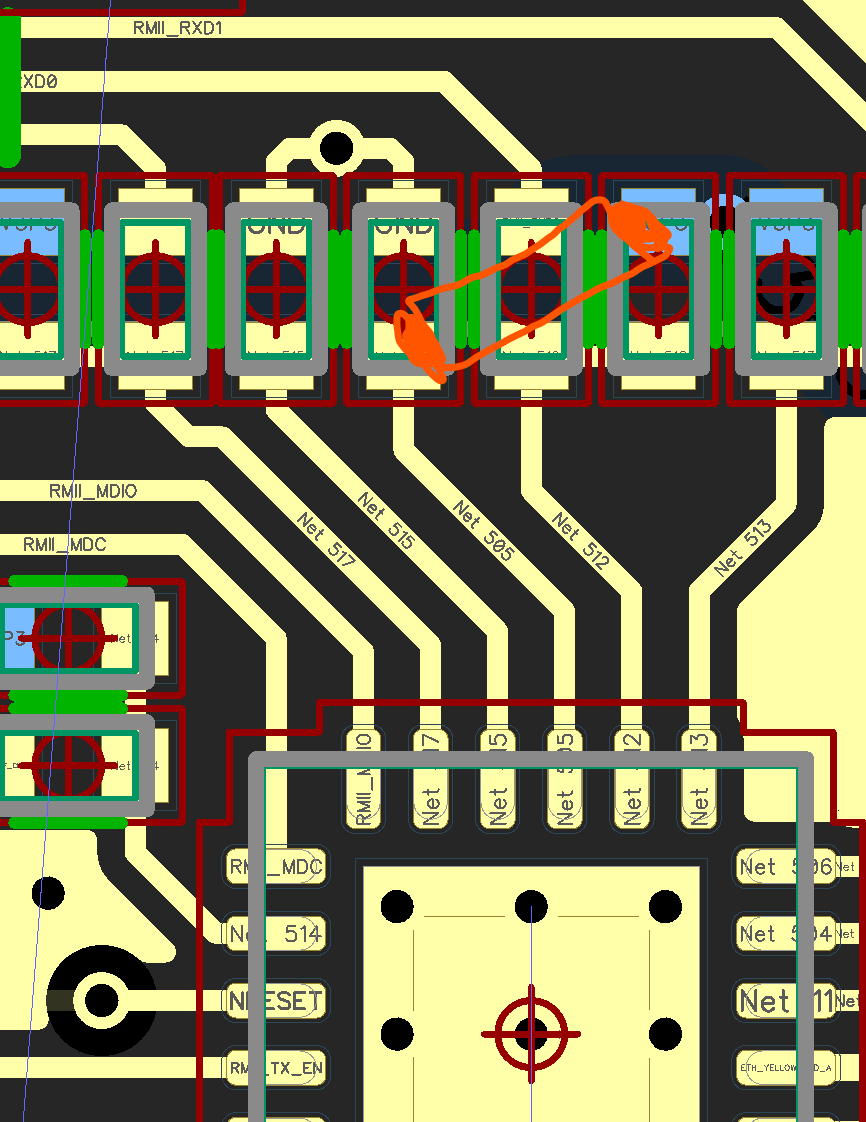
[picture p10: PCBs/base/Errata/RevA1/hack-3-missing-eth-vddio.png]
Hack 3


### Hack 4

Incompatible RJ45 combo jacks fitted to 10 prototype PCBs.  They are extremely difficult to remove due to the amount of
pins and the heat dissipation of the PCB.  PCB pre-heater needed before attempting removal.  It's easy to swap the IO
signals of the RJ45 connectors, but the LEDs are more complicated to fix because the traces are not easily accessible.

Even cutting the old connector off the board is extremely difficult due to the amount of  pins, shielding and plastic
inside the mag-jacks themselves.

Removal of the ACT/LNK header makes the top traces easier to cut and swap.

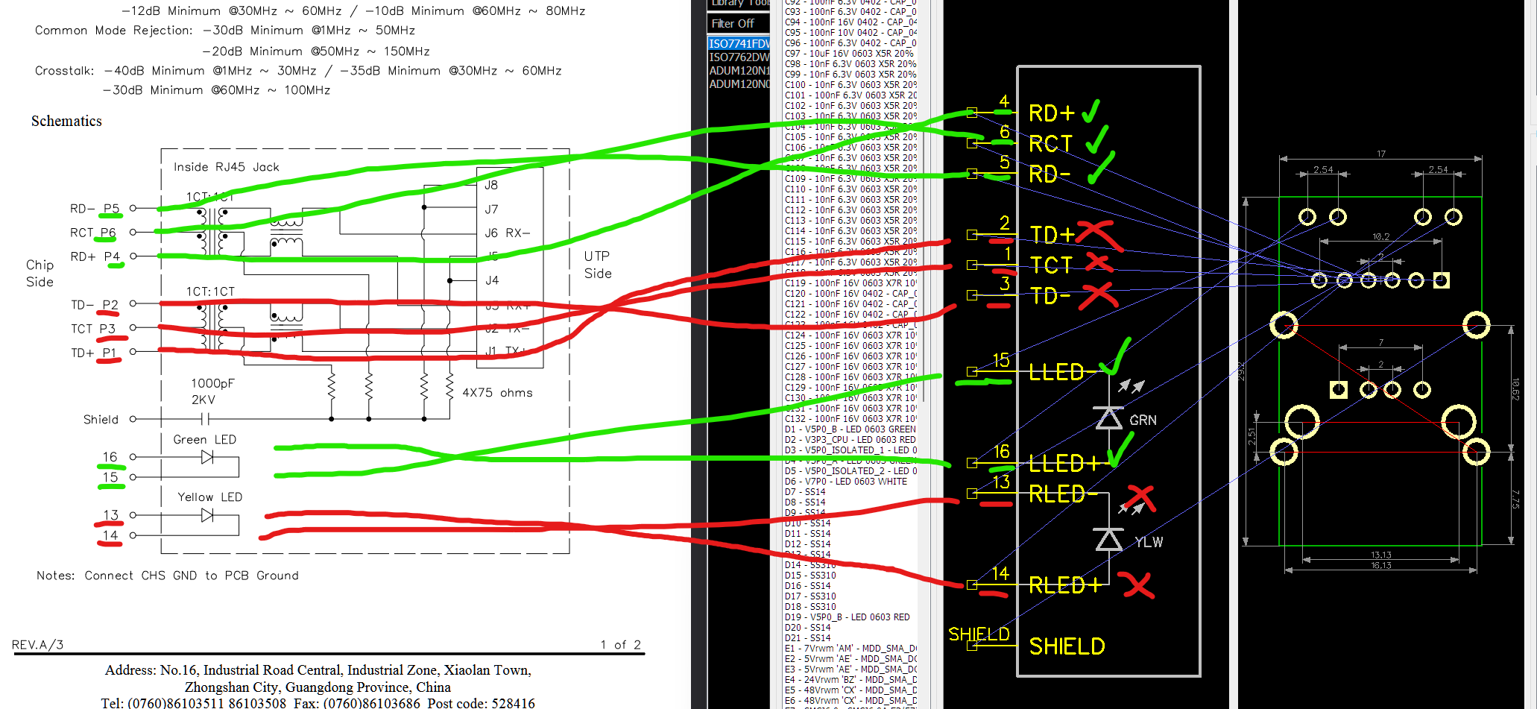
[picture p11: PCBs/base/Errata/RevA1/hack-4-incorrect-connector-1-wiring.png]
Hack 4

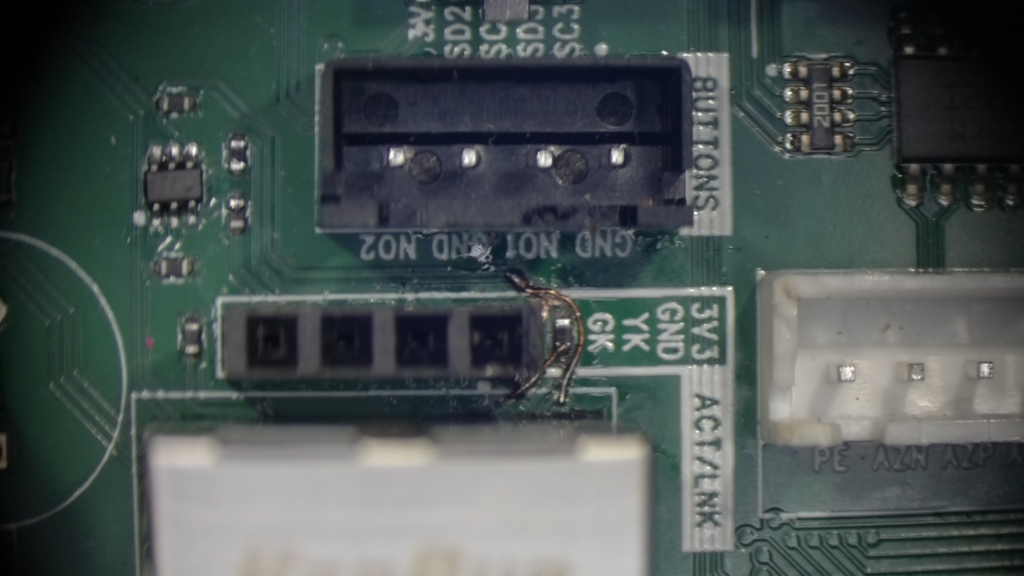
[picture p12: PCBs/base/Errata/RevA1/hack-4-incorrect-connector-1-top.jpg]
Hack 4

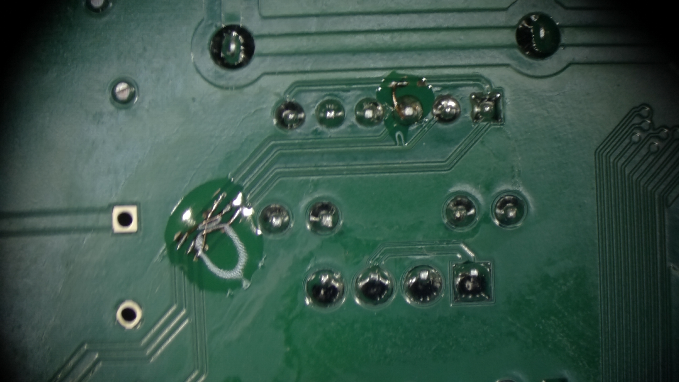
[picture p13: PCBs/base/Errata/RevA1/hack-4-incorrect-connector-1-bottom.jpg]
Hack 4


### Hack 5

Missing IO control of XYZ BCD EN signal.

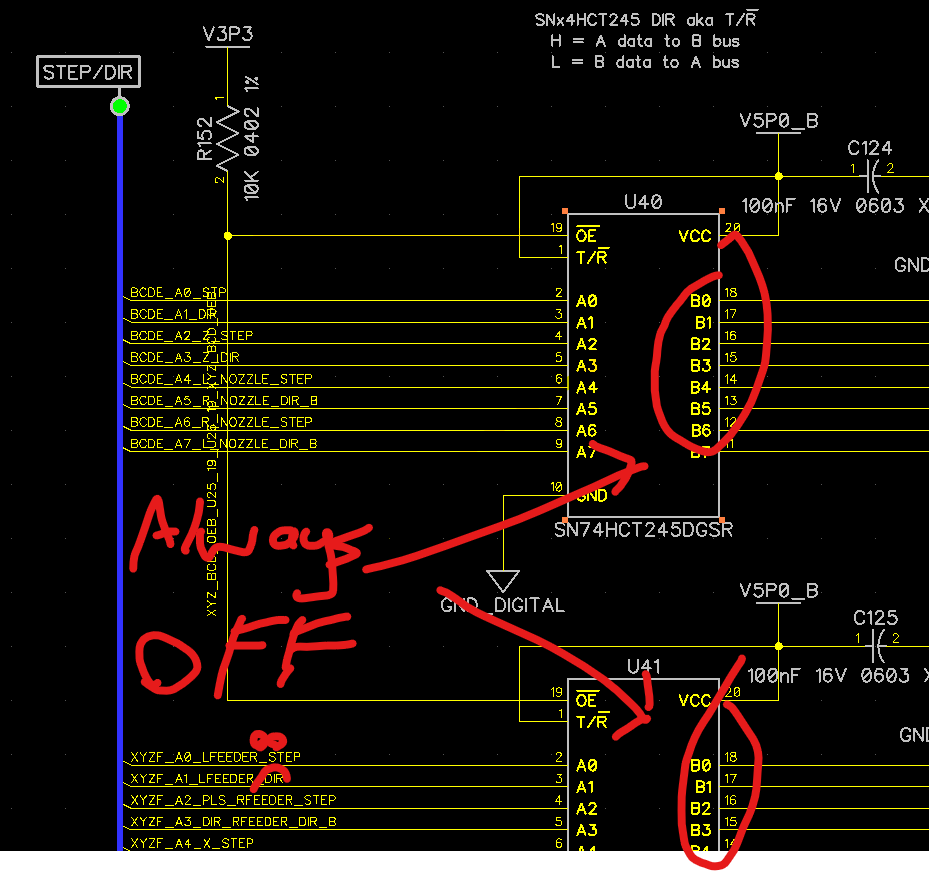
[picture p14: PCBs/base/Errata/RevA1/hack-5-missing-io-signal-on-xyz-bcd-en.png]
Hack 5


workaround-1:

Set the OE pin to LOW to enable the level shifters.  Remove the 10k pull-up resistor on the OE pin and connect the OE
resistor pad to GND via a 10k pull-down.

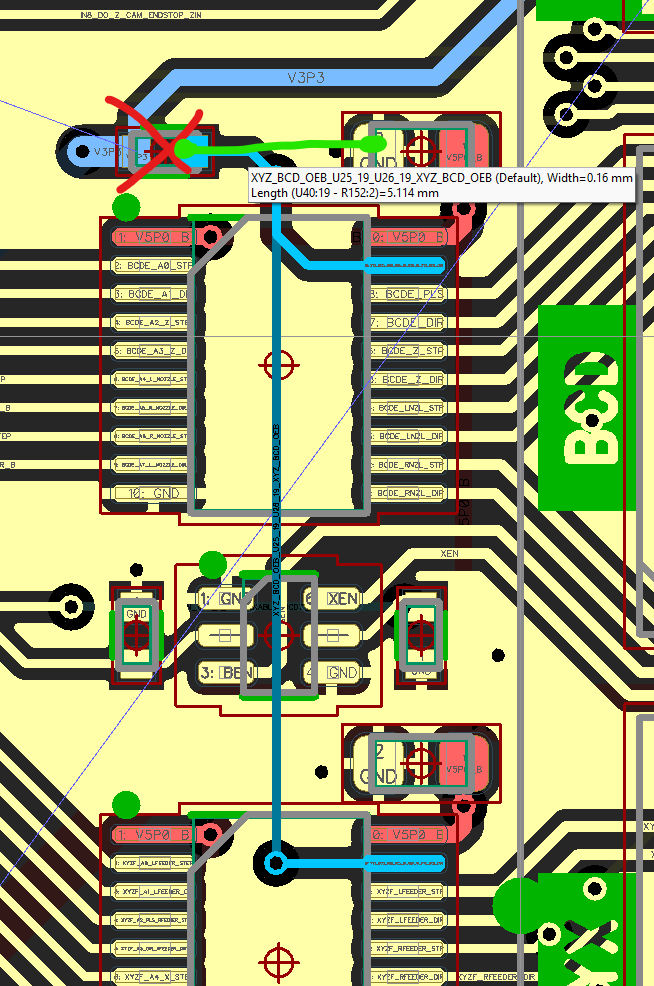
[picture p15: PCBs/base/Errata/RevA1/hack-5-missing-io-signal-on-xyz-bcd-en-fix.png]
Hack 5


# Rev B1

## Changes from Rev Ax

* Replace ADuM1200 with ADMuM120N0 to fix PM1-4 fail-safe state and power sequencing.
* Pull-downs on PM1-4 inputs (see ADMuM120N0 datasheet Rev F. Truth Table, Note 3.

 > Input pins (VIx) on the same side as an unpowered supply must be in a low state to avoid powering the device through the ESD protection circuitry

## TODO
[ ] use a single LM66200 instead of 2x LM66100, but ONLY if the chip handles ORing when both inputs are the same voltage for a long period.
[ ] add a pull-up to ~OE~ on U18 (SN74HCT245DGSR) to disable the device by default. without a core board attached the inputs are floating and undefined. See section 11.1 in the SN74HCT245DGSR datasheet.
[ ] fix missing VDDIO on U20:9
[ ] fix missing MCU/FPGA control of XYZ BCD EN signal.
[ ] change USB-Ext header connector to use the same connector as the CHMT's USB socket's wire.  5-pin. socket.

## Investigations

### LM66100 ORing priority

Thursday, May 7, 2026 9:28 PM
```
commanderguy3001:
enabled if VIN > CE + 250mV
ST to GND if VIN < CE - 80mV

say both 3V3 rails come on at the same time.
U5:CE would be at 3.3V
U5:VIN is at 3.3V
so U5 is disabled
U5:ST is grounded
pulling U6:CE to ground, enabling it in "all" cases

commanderguy3001: yeah it's opposite to how they explain it in the DS.

say U5:VIN comes on first
U5:CE is at/near GND
enabling U5
making ST high-Z, so pulled up to U5:VIN
then let's make U6:VIN come on with the exact same voltage
since CE and VIN are the same on both chips, U5 stays enabled, and U6 stays disabled
now we add some noise to our inputs
at some point, U5:CE is gonna be more than 80mV below U5:VIN, disabling U5
this makes U5:ST go low
which turns on U6
```

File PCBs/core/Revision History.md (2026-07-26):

# Rev A1

## Errata

### issue with MCU and FPGA activity LEDs.

On initial power up, the MCU and FPGA activity LEDS, are sometimes bright, sometimes faint, but never off.

No workaround / solution developed yet.

### FPGA starts on power-up.

After some consideration, the FPGA should NOT start up on power-up, but only after the MCU drives CRESET_B high.
Currently there is a pull-up on CRESET_B which makes the FPGA load it's program from flash on boot.

#### Workaround

Reposition R107, remove it from the board, stand it on it's side, and place it diagonally between pad C148:2 (GND) and pad R107:2 (CRESET_B). Pad R107:1 (V3P3/VCCIO_2) should not have any component connected to it.

This will change the pull-up to a pull-down and prevent the FPGA from booting up when power is applied. The MCU now has
to drive CRESET_B high and keep it high to make the FPGA boot.

### FPGA does not boot from flash.

The FPGA waits in SPI slave mode to be programmed, instead of booting from flash as originally intended.

This was due to a misunderstanding of the FPGA documentation due to bad wording in the hardware checklist manual.

#### Workaround

Remove R131, move it between pad R107:1 (which will be empty after applying the other workaround above) and pad J405:13.

This will make the FPGA boot from flash when the CRESET_B pin is pulled high by the MCU.

### Power supervisor prevents regulators from starting up.

The power supervisor (TPS3820-50DBVx) prevents the regulators from starting up.

#### Workaround

a) Bypass it by cutting the PGOOD trace on the bottom of board then jumper C2:1 to U2:1 

or

b) replace with a TPS3820-33DBVx which has a lower threshold.

### Missing SEL default signals for MUX_SEL1-4

The FPGA drives signals high when under RESET or when pins are not configured.
The SN3257 switches have internal 6Mohm internal pull down to GND.
The voltage is the not well-defined, so stronger external pull-down resistors should be used.

#### Workaround

Fit 4x 10Kohm pull-down resistors

* U301:1 (SEL) MUX_SEL1 to C301:2 GND.
* U302:1 (SEL) MUX_SEL2 to C302:2 GND.
* U303:1 (SEL) MUX_SEL3 to C303:2 GND.
* U304:1 (SEL) MUX_SEL4 to C304:2 GND.

## Problems

### ESP-C6 module not working.

The ESP-C6 modules did not reflow properly, many of the pins were unconnected.  Likely less paste is needed under the
four corner pads and under the center pads so that the module sits lower to the board.

#### Workaround

1. Ensure SD card and platic connectors are covered with heat-resistant tape.
2. Remove the module.
3. Inspect the pads on the module, take photo.
4. remove the high-temperature solder from the board and module using solder wick.
5. Apply flux to the module, tin the IO pads on the module with low-temperature solder, but not the thermal pads 
   or the 4 corner pads.
6. Apply solder to the module IO pads on the PCB, but not the thermal pads or the 4 corner pads.
7. Reflow the module, note it will self center strongly, ensure it floats back into position.
8. Allow the solder to cool and solidify brielfly.
9. Press down on the module and reflow it, being careful not to let it move.
10. Allow the solder to cool and solidify, then remove pressure.
11. Power on the board, hold down ESP BOOT button, connect USB cable. Ensure USB devices are enumerated.
12. If not replace the module for a new one and re-test.

# Rev B1

## Changes from Rev A1

* Use TPS3820-33DBVx instead of TPS3820-50DBVx for the power supervisor. 
* Changed the pull-down on SPI_SS_B to a pull-up so the FPGA default behavior is to boot from flash when reset.
  Note: The MCU can still drive SPI_SS_B low, then set CRESET_B high so make the FPGA wait in SPI slave mode.
* Changed the Paste for the ESP-C6 module
  * Only center pad has paste, but 15% fill
  * Corner pads have the same volume of paste as the signal pads. 40% fill.
  * All module solder pads have defined paste settings, previously they were all default.
* Changed the silkscreen outline of the ESP-C^ module so it's easier to confirm alignment.
* Changed the pull-up on CRESET_B to a pull-down to keep the FPGA disabled until the MCU turns it on.

## TODO

### CRITICAL

[ ] don't fit R1 V5EN by default
[ ] fix MUX_SEL[1-4] defaults.
[ ] ensure that pins that are always used together in verilog code are on the same IO banks and next to each other to avoid
    on-chip routing delays.  candidates include
    * the port clock, wake, int signals.
    * quad spi IO0-3.
    * tim mux select 0-3.
    * i2c mux select.
    * adc address select.
    * stepper bcde (4 step, 4 dir)
    * stepper xyzf (4 step, 4 dir)
    * digital inputs DIN1-8
    * pwm outputs OT1-8
    * LA0-15

### Would-be-nice

[ ] reduce LED brightness of the green LEDs.
[ ] fix the MCU and FPGA activity LEDs so they are not randomly ON or dim by default.  perhaps by adding pull-downs
    to the FPGA output pins.
[ ] add a warning triangle and 'see manual' next to the V5EN resistor jumper.

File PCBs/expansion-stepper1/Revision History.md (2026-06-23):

# Rev A1

## Errata

### Power sequencing on drivers
 
The drivers are not correctly disabled when stepper motor power is applied before the core / base board power.

#### Workaround

* Remove R31, set aside.
* Connect the removed R31 10k resistor between either:
  a) U7:12 (OUTD) WAKE_1 and U7:16 (VCC2) V5P0_IO.
  b) TP14 WAKE_1 and R51:1 V5P0_IO

### Transposed FET input/feedback signals

There is an issue with the FET input circuits not matching the feedback circuits, 1 -> 2 and 2 -> 1 instead of
1 -> 1 and 2 -> 2.

#### Workaround

Either swap the BMA1 with BMA2 and BMB1 with BMB2 or swap HA1 with HA2 and LA1 with LA2.

In practice, it's easier to do the latter, since the former requires cutting traces that are next to pads which is
more difficult.

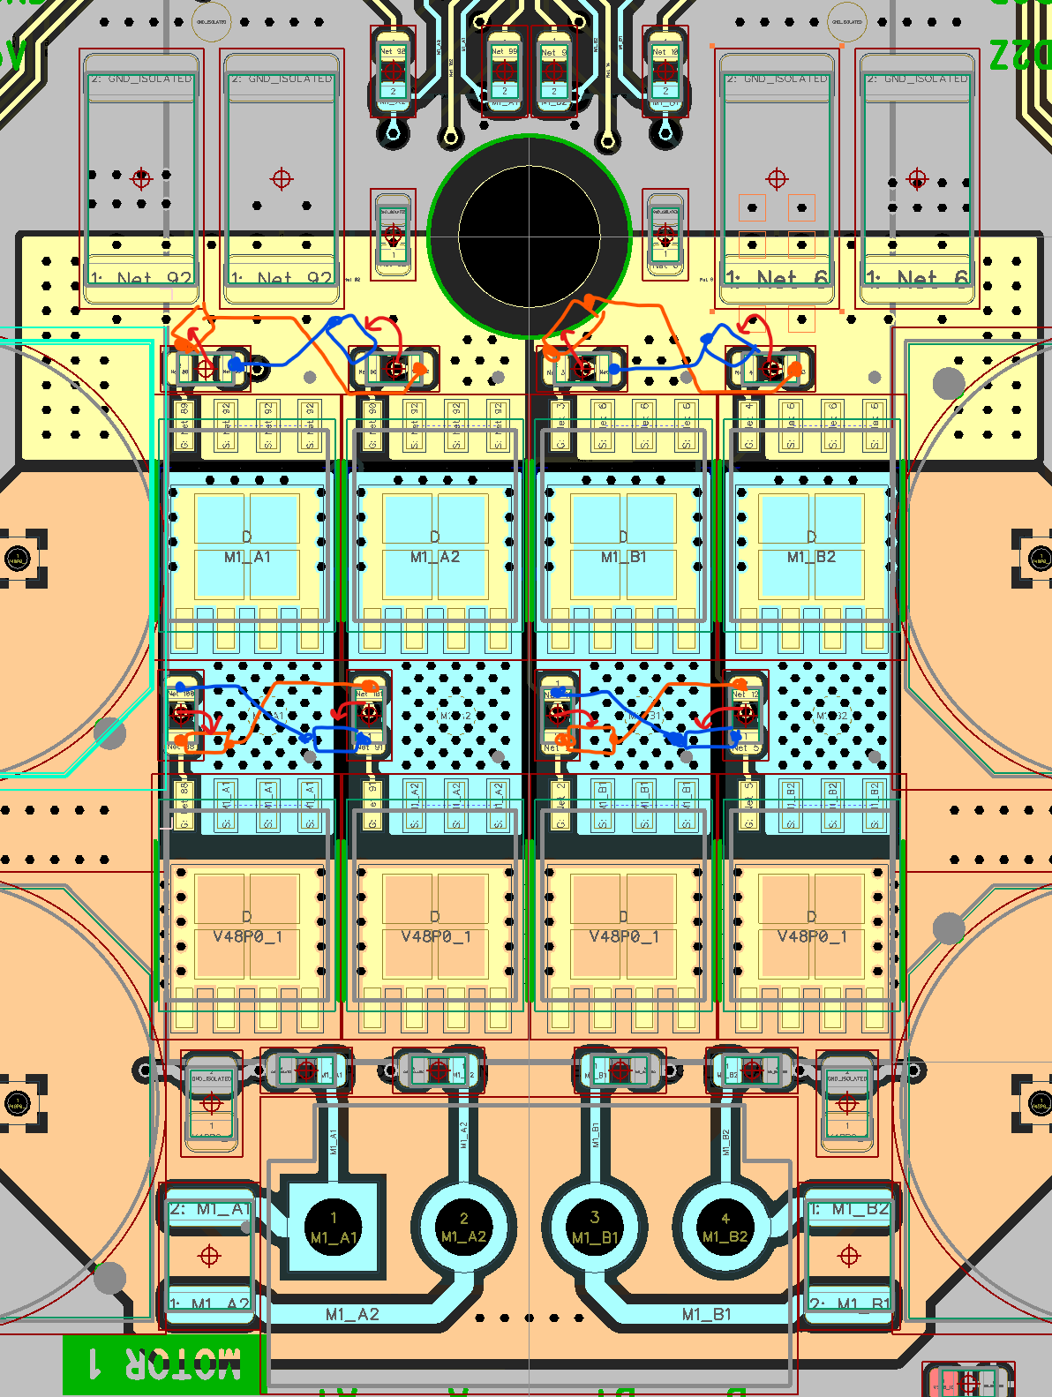
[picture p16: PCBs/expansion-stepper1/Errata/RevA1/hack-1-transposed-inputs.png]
Hack 1


Example rework

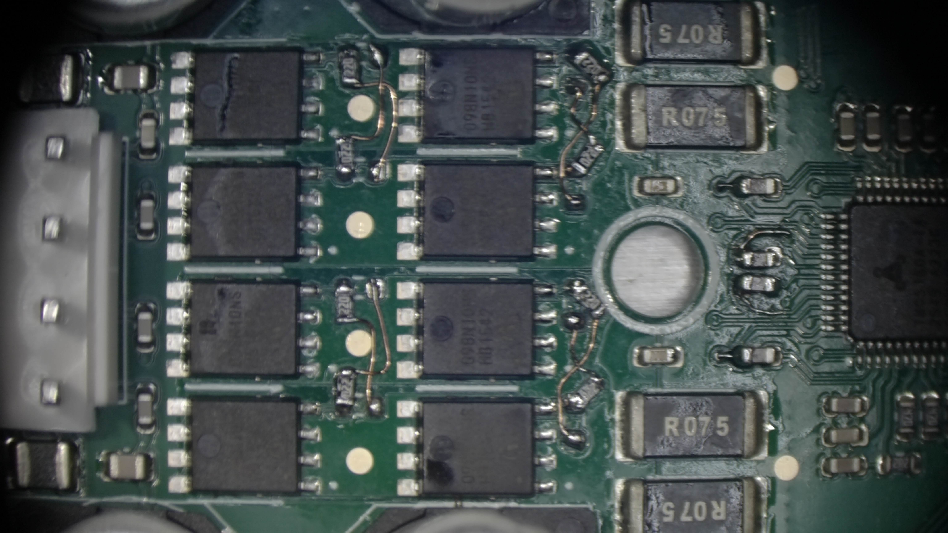
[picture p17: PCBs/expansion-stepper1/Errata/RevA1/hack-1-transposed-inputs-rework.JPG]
Hack 1


This need to be done for BOTH of the TMC5160.  So 16 jumper wires per board are required, but no trace cutting.

# Rev B1

## Changes from Rev A1

## TODO

### CRITICAL

[ ] Swap HA1 with HA2 and LA1 with LA2 to match the rework.
[ ] Move the DRV_ENN pull-up resistors to the opposite side of the signal isolators, so they are on the same side
    as the TMC drivers chips.
[ ] Ensure variant does not have the NO_PLACE components fitted (R25, R50, etc)
[ ] Fix E2 component, should be a 12V TVS diode, not 7V. Use MDD SMAJ12A (C113957) not SMAJ7.0A (C138782)
[ ] Add missing silk screen for motor pinouts nearest the edge connector.

### Would-be-nice

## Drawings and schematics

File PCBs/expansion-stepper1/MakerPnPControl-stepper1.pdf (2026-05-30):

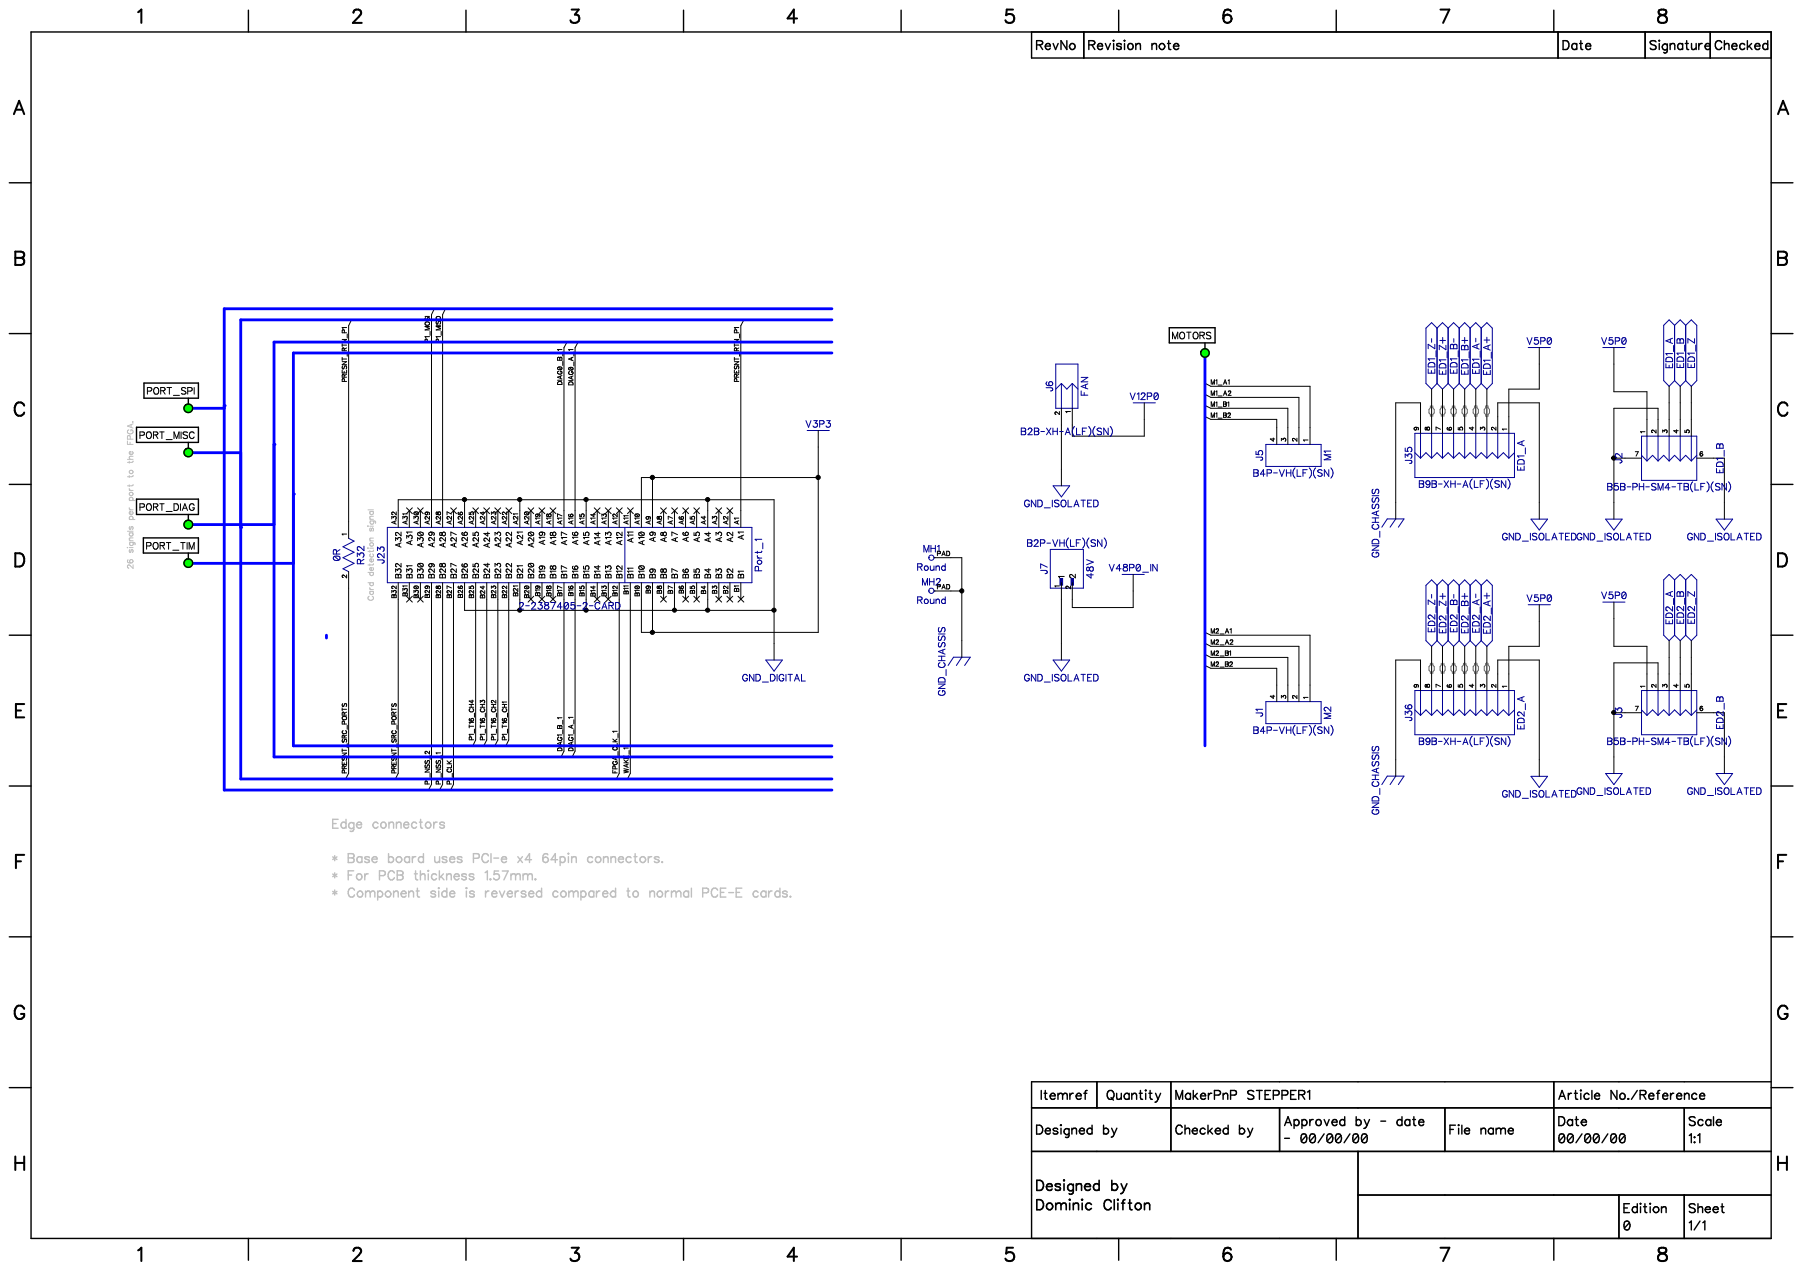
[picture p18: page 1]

B2B-XH-A(LF)(SN) FAN

26 signals per port to the FPGA.
PORT_MISC

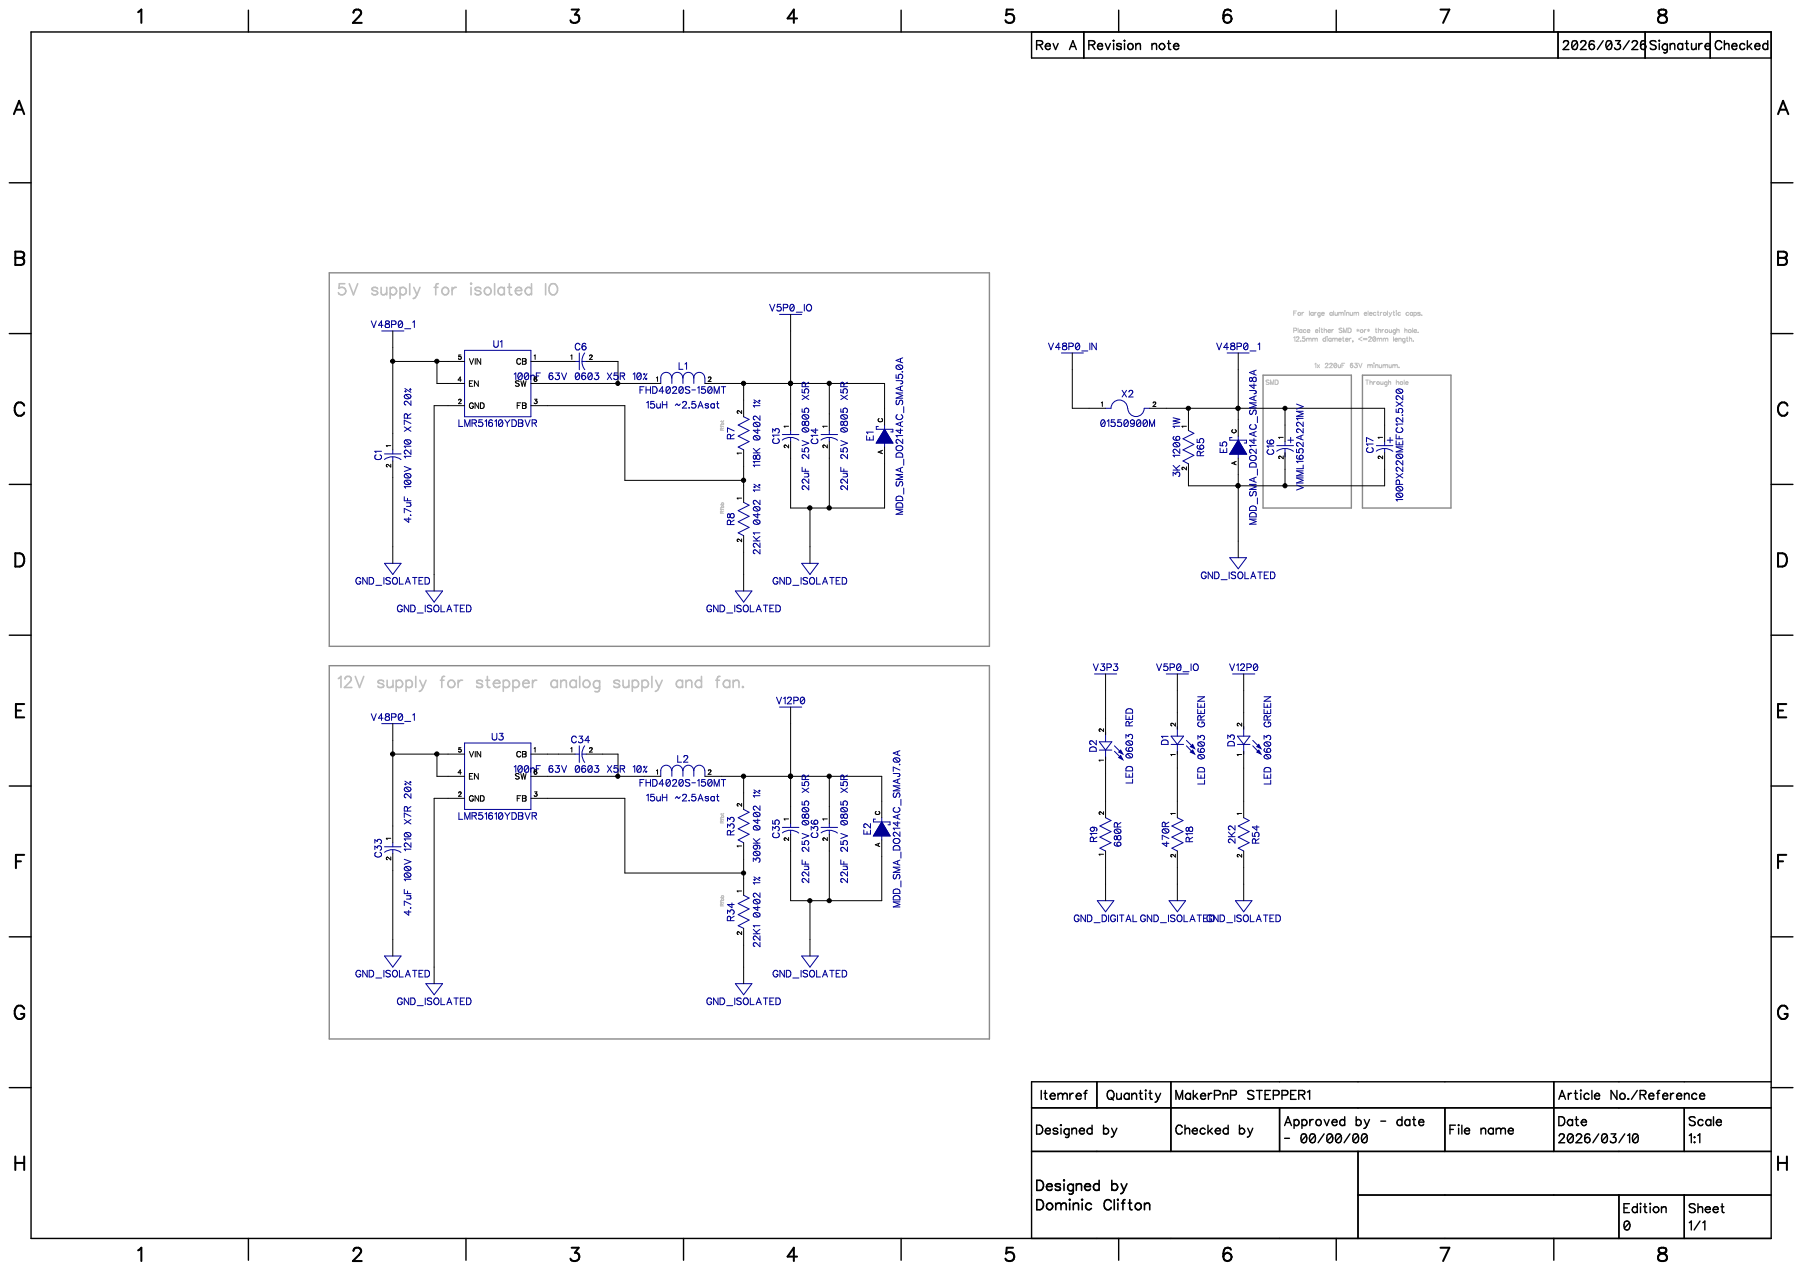
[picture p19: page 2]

5V supply for isolated IO

For large aluminum electrolytic caps.

Place either SMD *or* through hole.
12.5mm diameter, <=20mm length.

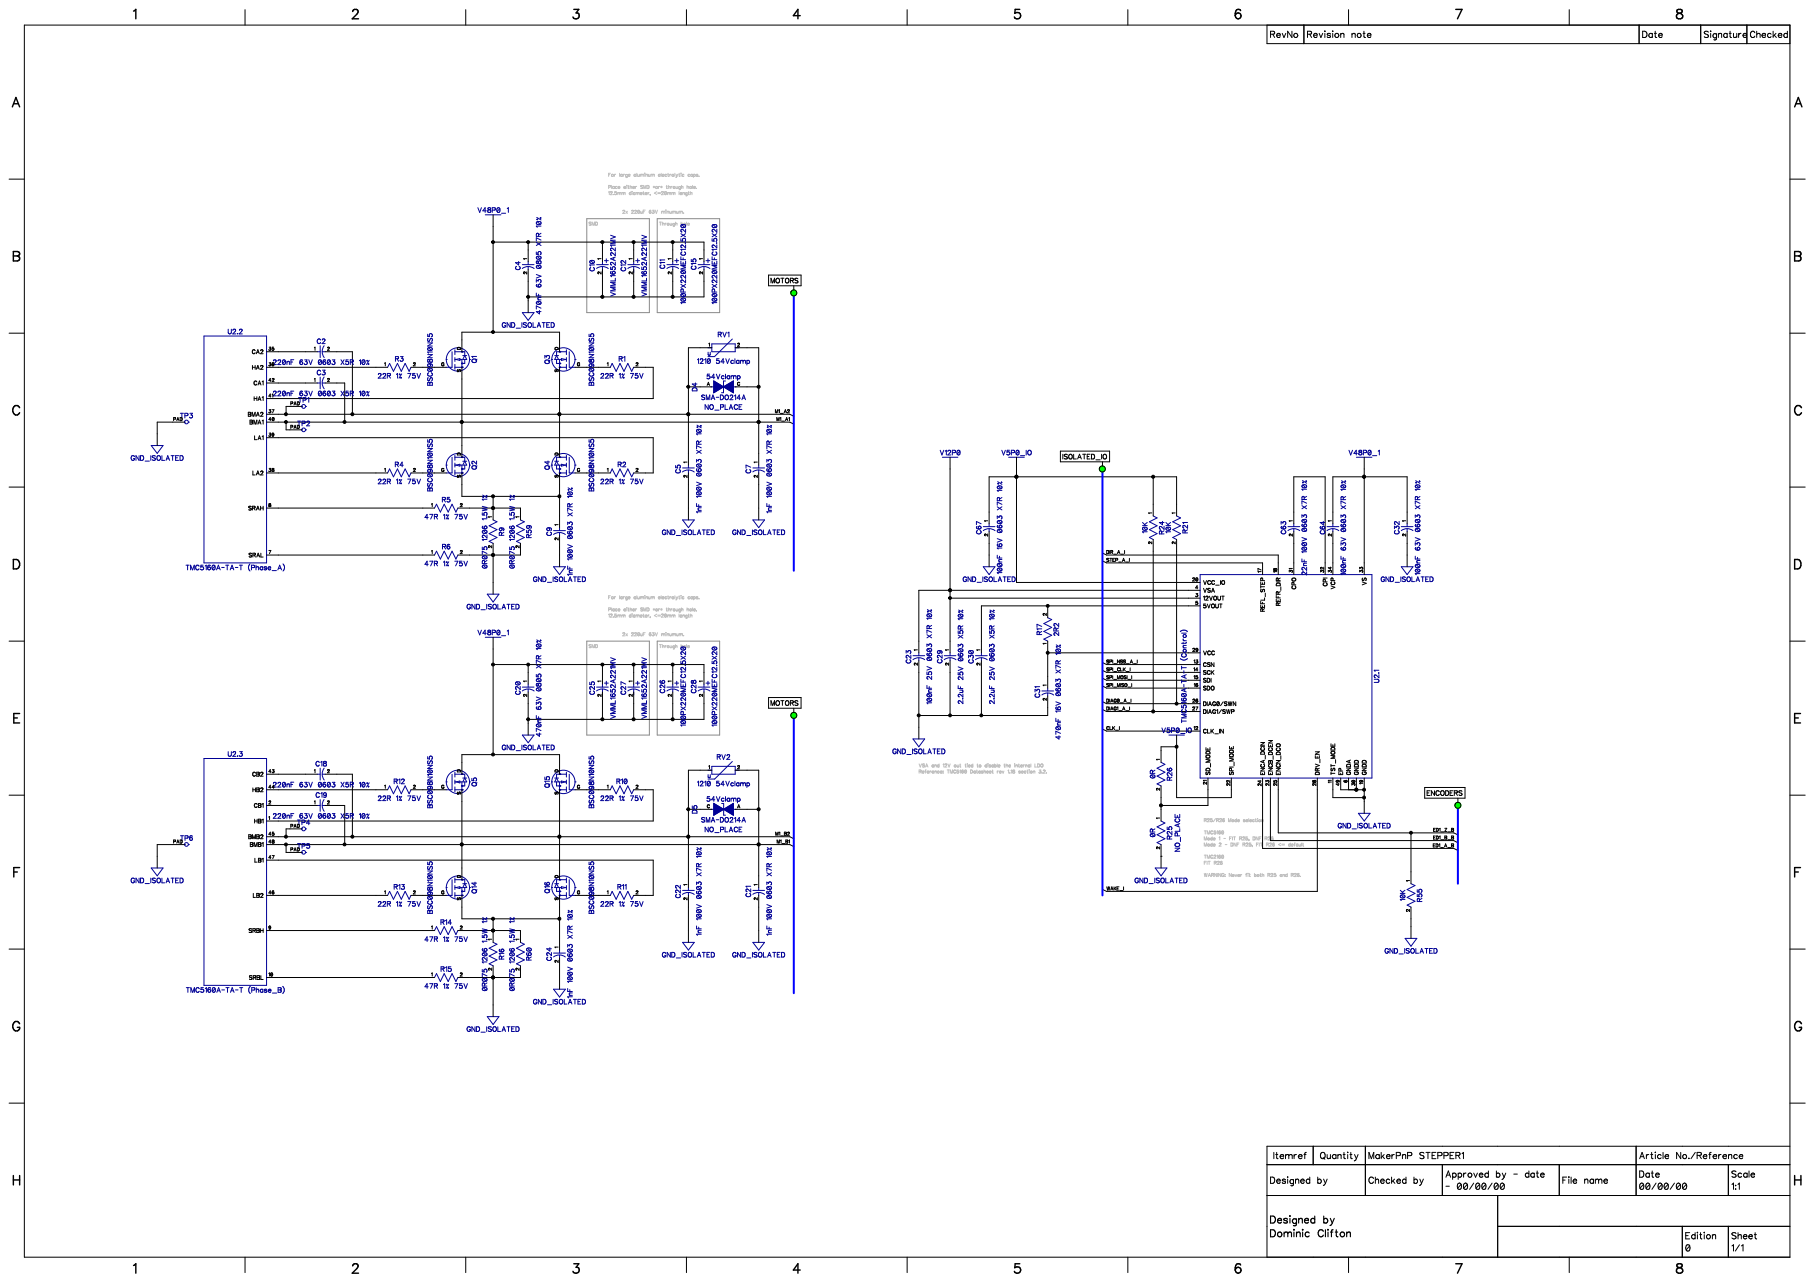
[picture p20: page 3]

For large aluminum electrolytic caps.
Place either SMD *or* through hole.
12.5mm diameter, <=20mm length

TMC2160
FIT R26
WARNING: Never fit both R25 and R26.

Designed by Checked byApproved by - date

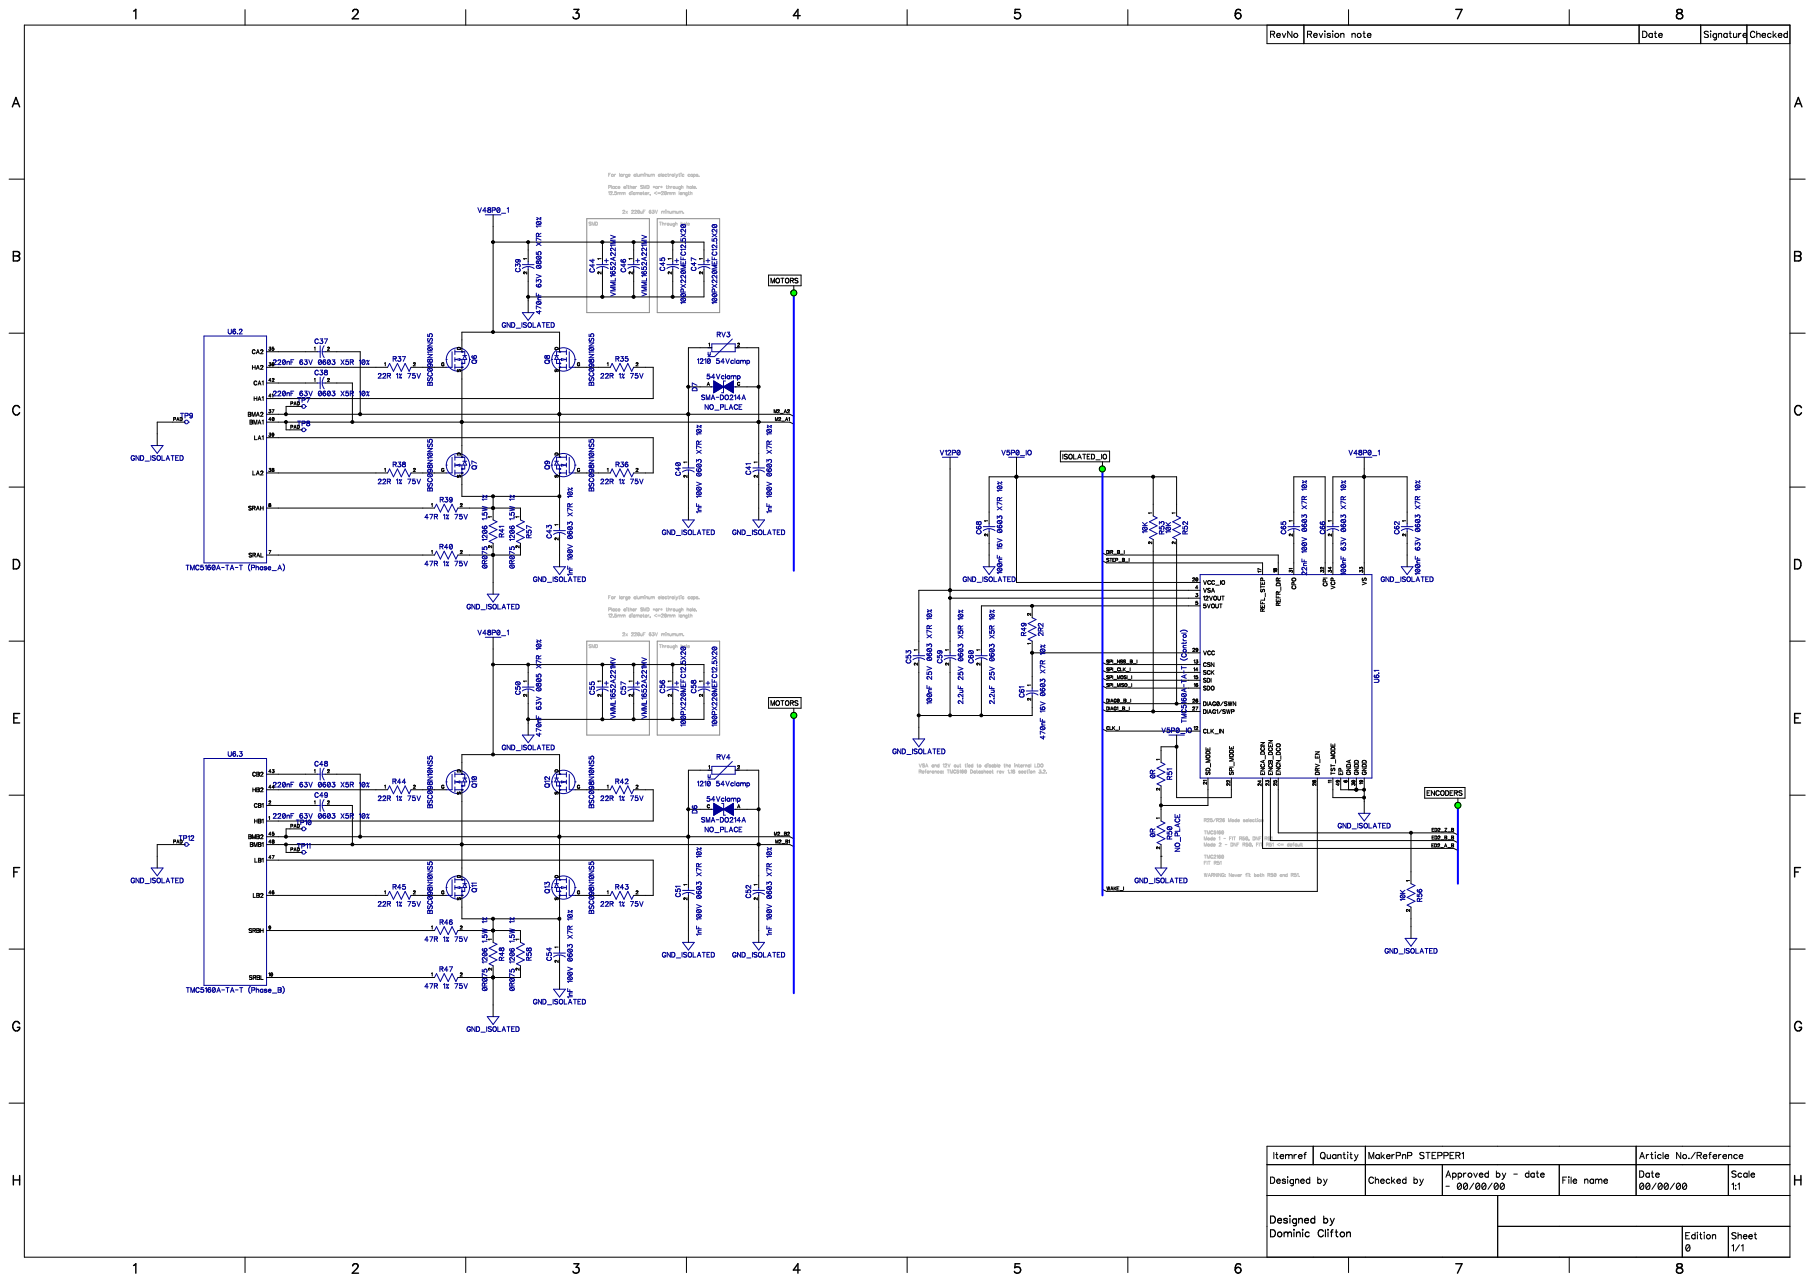
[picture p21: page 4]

For large aluminum electrolytic caps.
Place either SMD *or* through hole.
12.5mm diameter, <=20mm length

TMC2160
FIT R51
WARNING: Never fit both R50 and R51.

Designed by Checked byApproved by - date

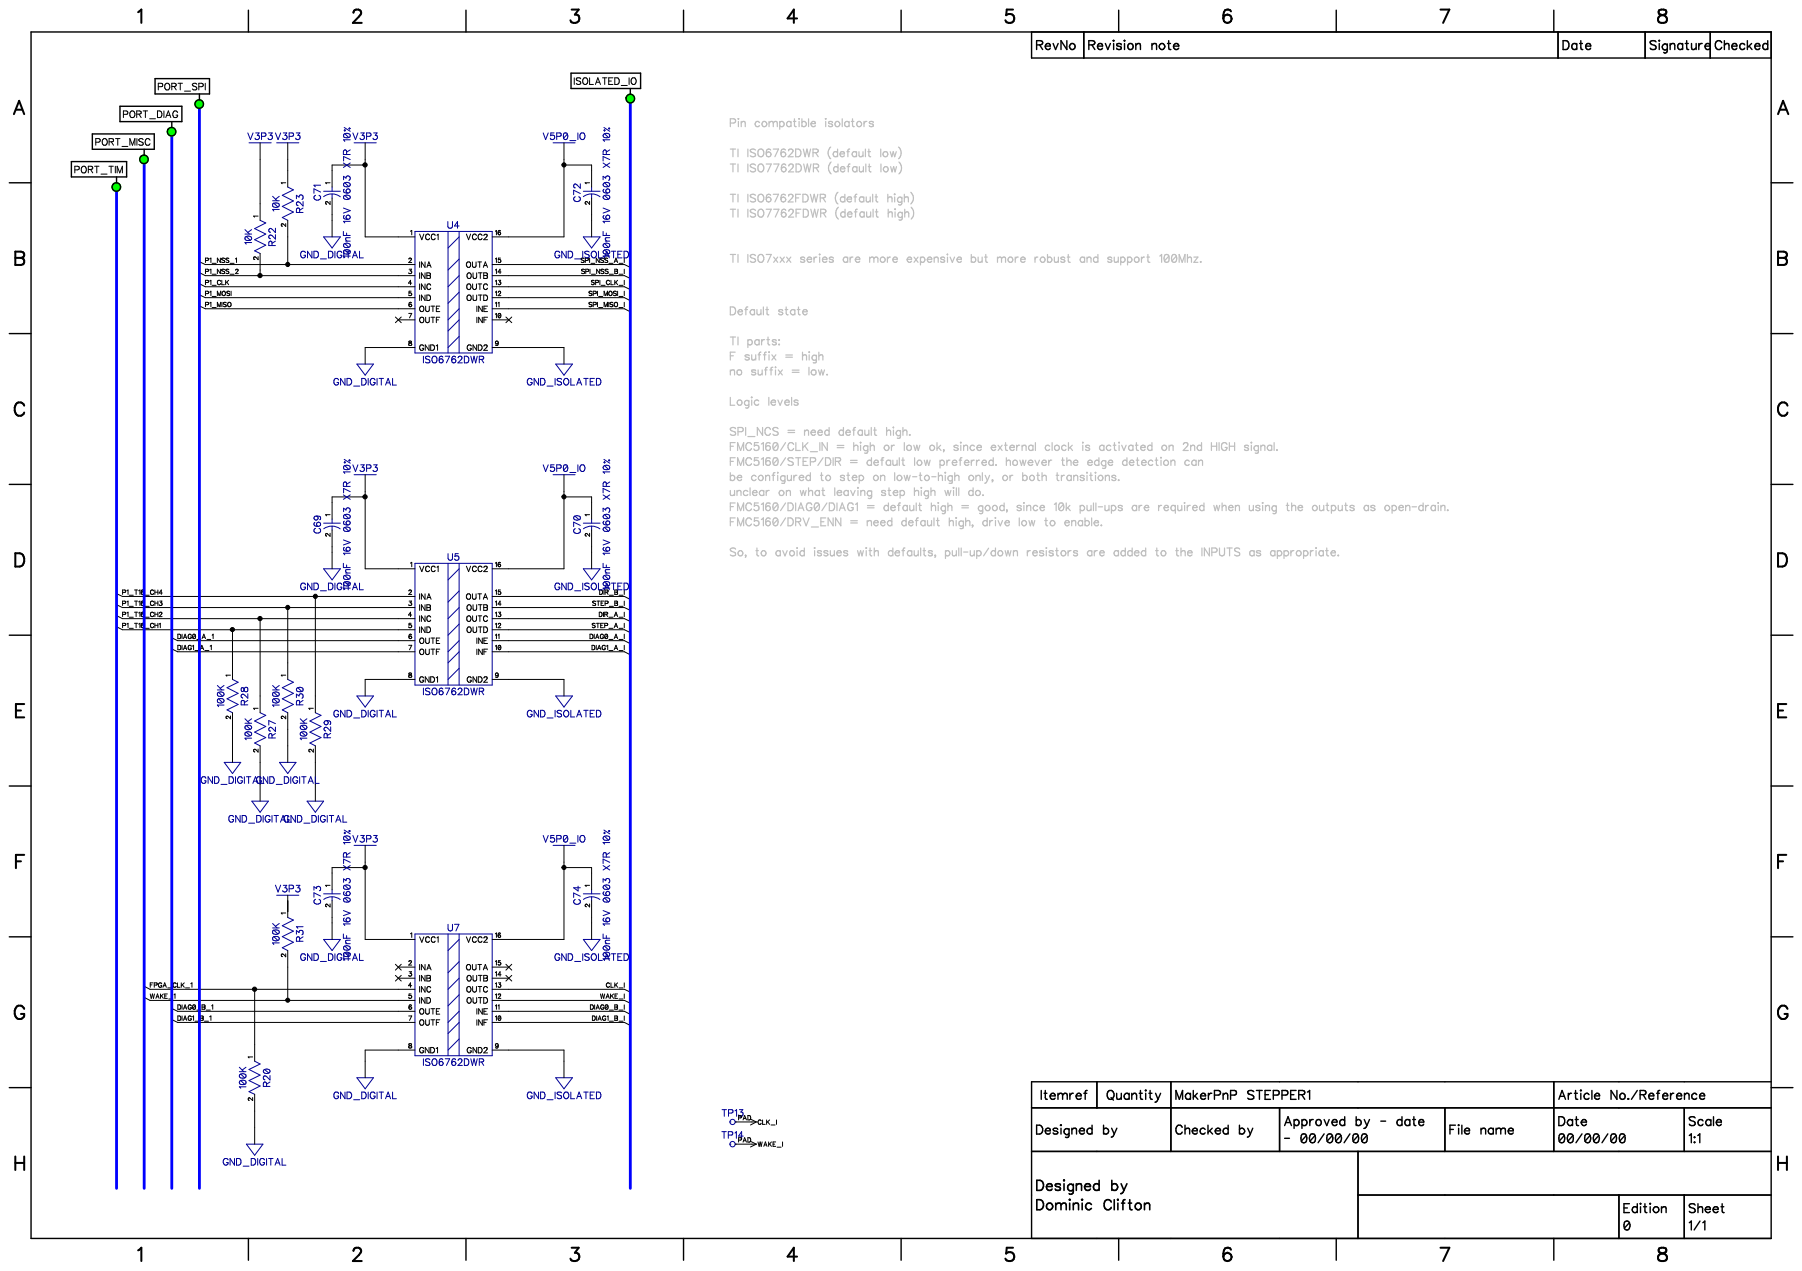
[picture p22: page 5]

TI ISO7xxx series are more expensive but more robust and support 100Mhz.

INF 10 INE 11 OUTD 12 OUTC 13 OUTB 14 OUTA 15

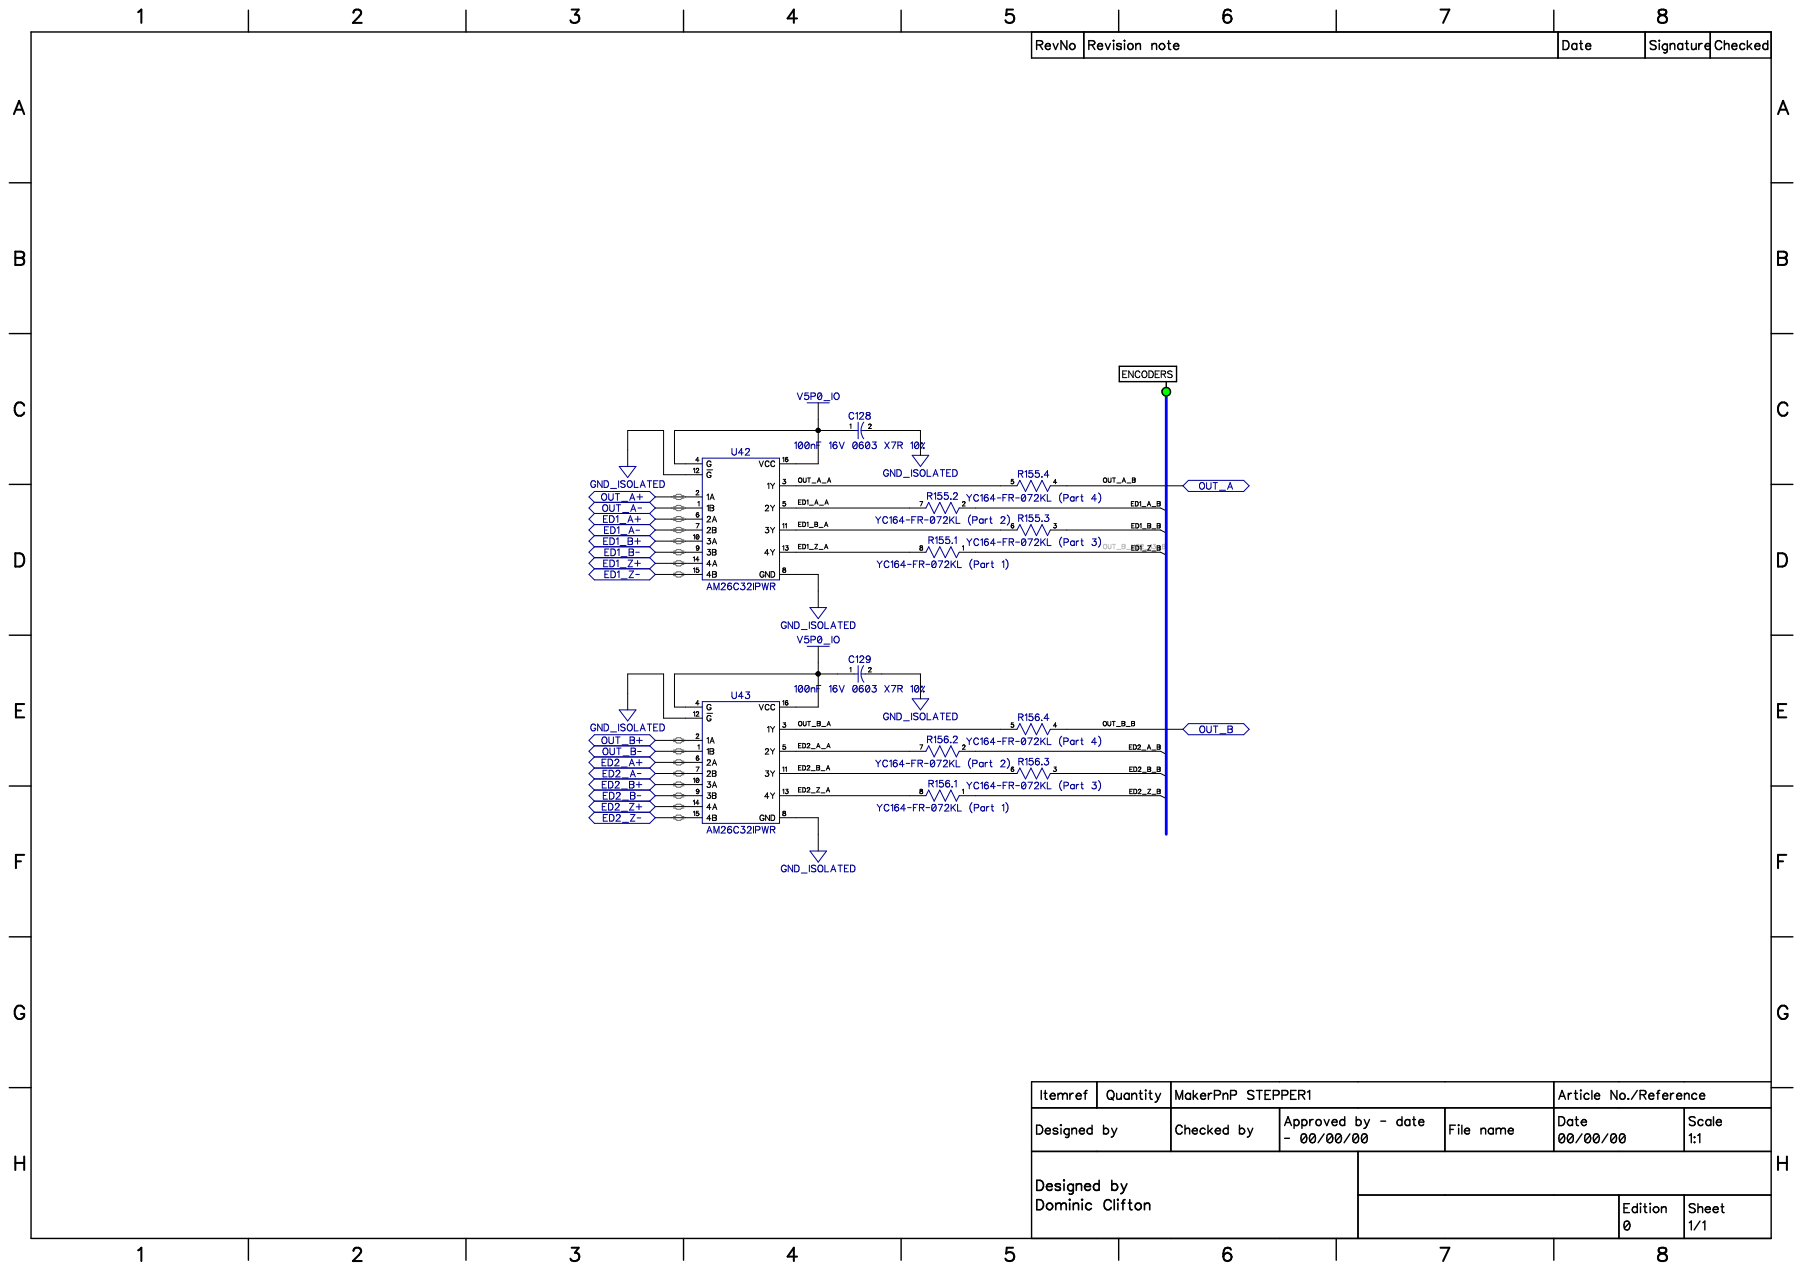
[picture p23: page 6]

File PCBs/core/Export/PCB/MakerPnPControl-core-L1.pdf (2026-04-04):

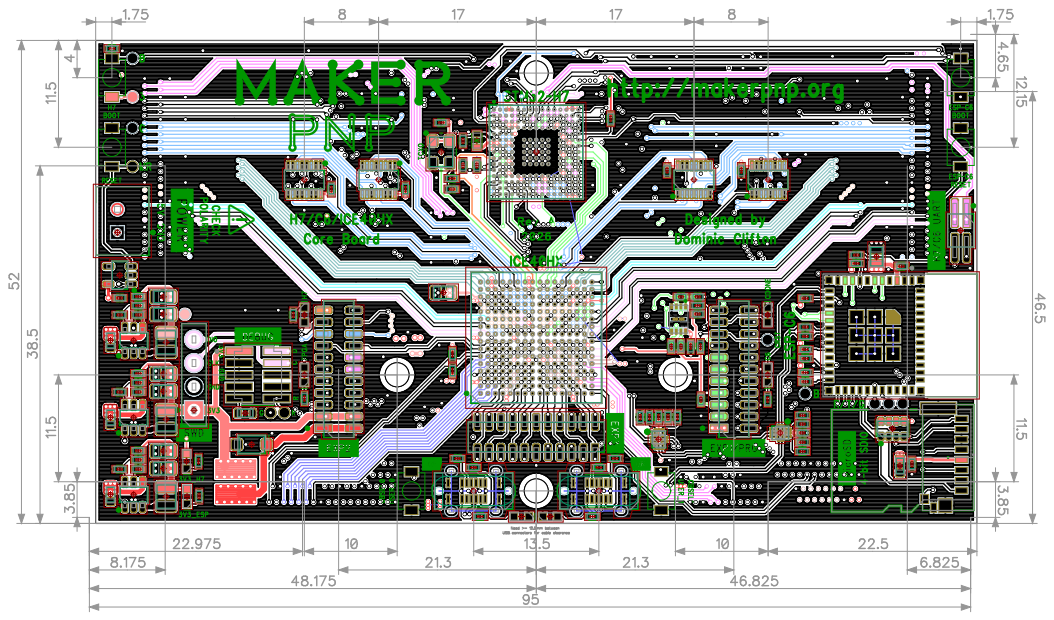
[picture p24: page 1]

Need >= 12.5mm between
USB connectors for cable clearance

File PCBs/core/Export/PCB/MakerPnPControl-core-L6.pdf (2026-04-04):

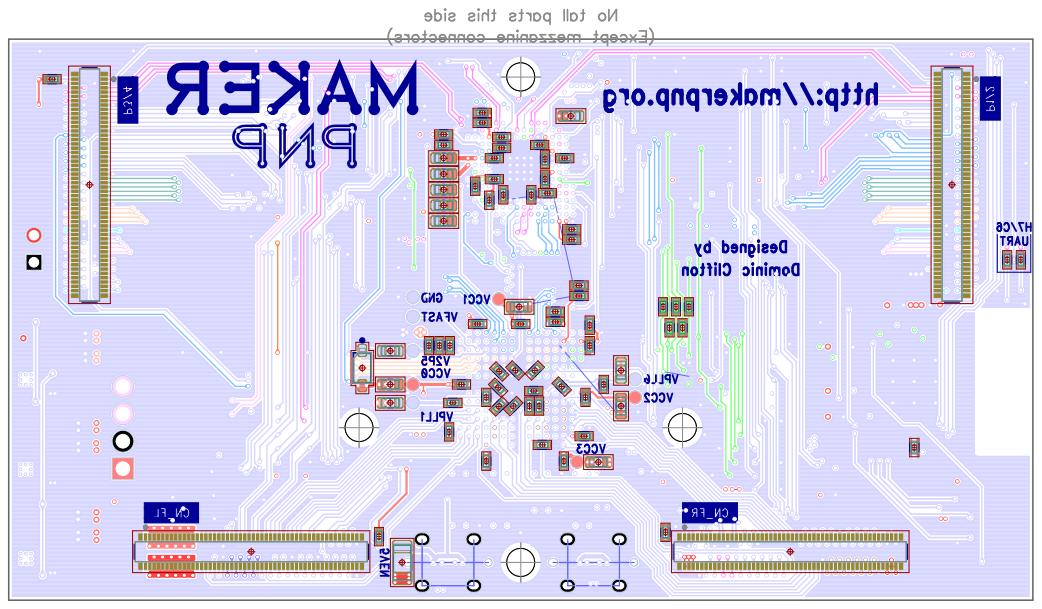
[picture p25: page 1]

No tall parts this side
(Except mezzanine connectors)
PNP MAKER

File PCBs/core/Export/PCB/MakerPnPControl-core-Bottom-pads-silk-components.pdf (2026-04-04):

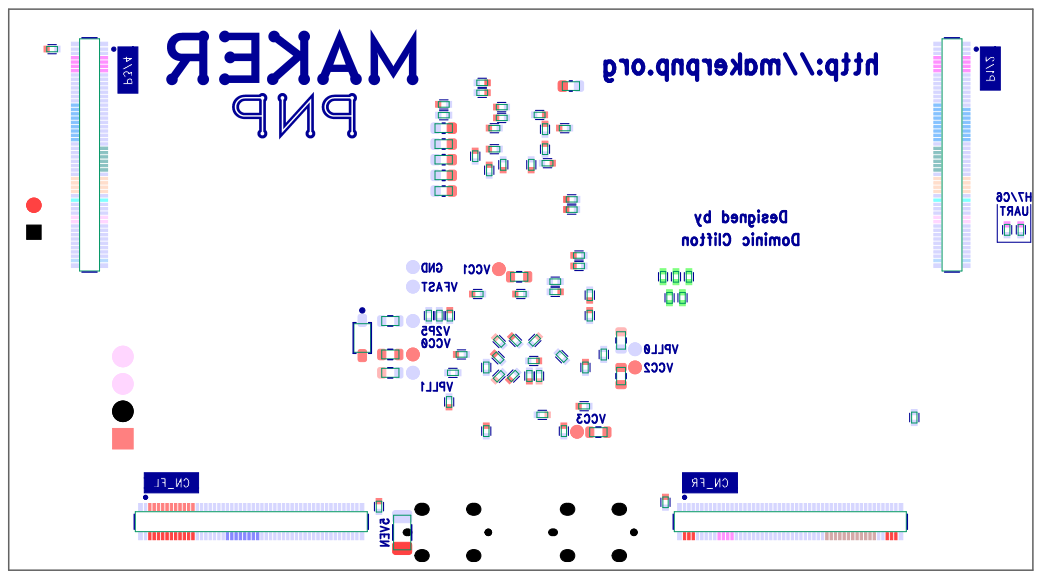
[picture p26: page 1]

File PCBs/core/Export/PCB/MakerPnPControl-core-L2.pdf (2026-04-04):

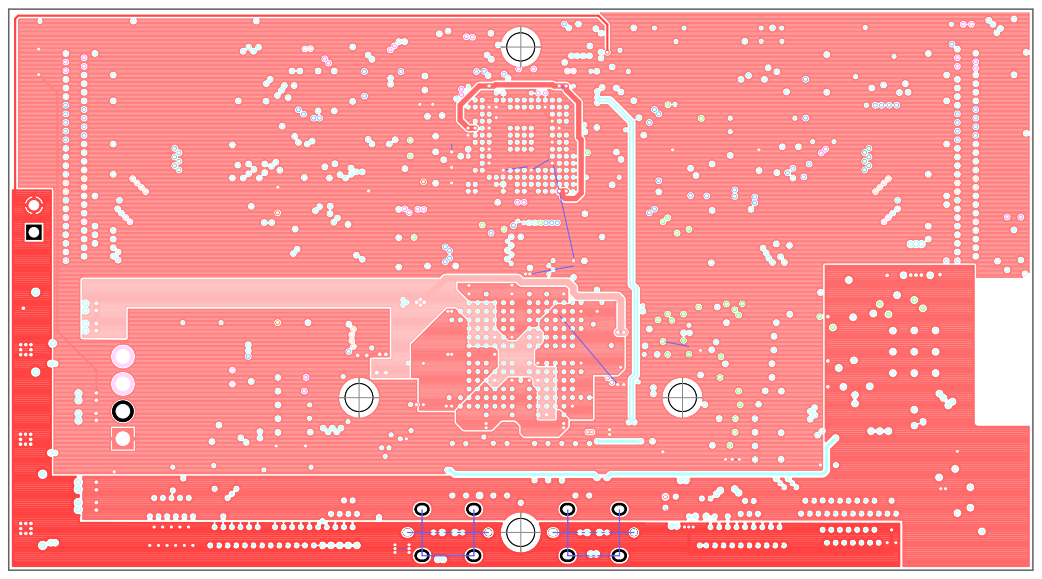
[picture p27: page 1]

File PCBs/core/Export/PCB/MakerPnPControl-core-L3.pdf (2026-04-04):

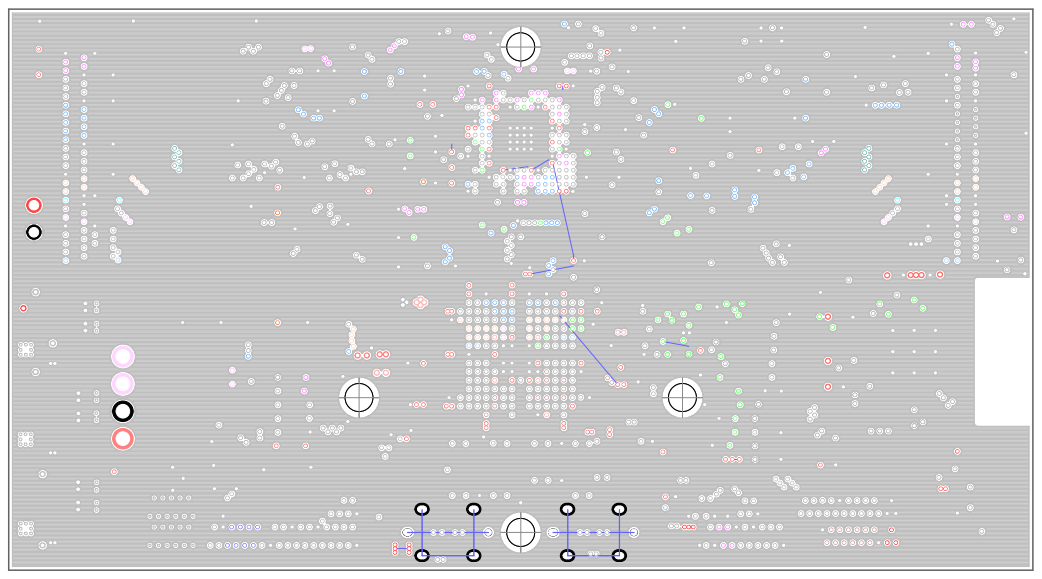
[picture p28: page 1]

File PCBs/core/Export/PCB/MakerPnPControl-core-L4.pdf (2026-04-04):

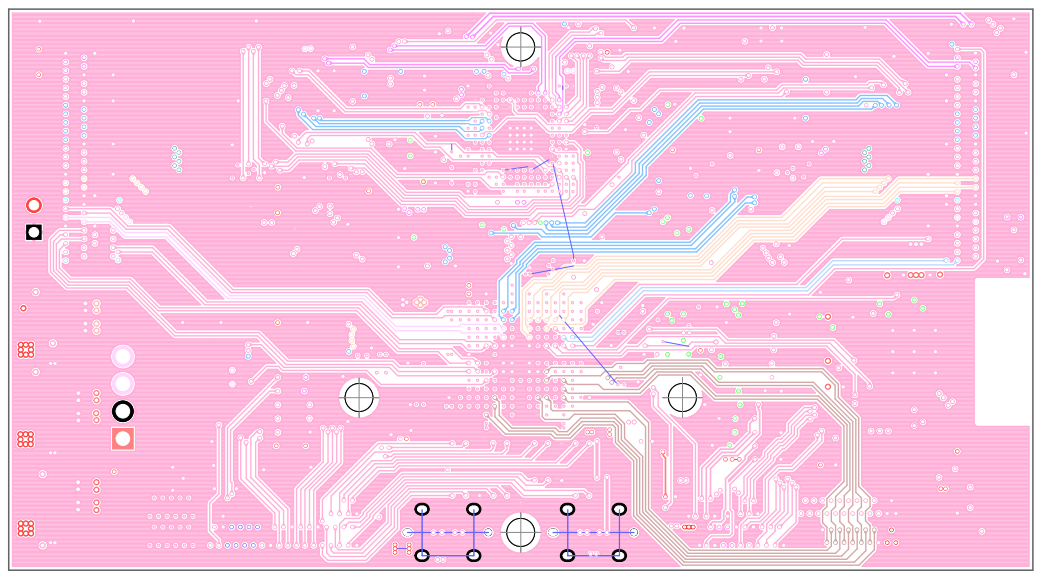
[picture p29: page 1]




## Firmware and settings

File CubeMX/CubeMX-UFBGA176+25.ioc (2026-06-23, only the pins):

Mcu.UserName=STM32H725IGKx
PA0.Signal=S_TIM2_CH1_ETR
PA0_C.GPIO_Label=ANALOG_IN_1
PA0_C.Signal=ADCx_INP0
PA1.Signal=ETH_REF_CLK
PA10.Signal=USART1_RX
PA11.Signal=USB_OTG_HS_DM
PA12.Signal=USB_OTG_HS_DP
PA13(JTMS/SWDIO).Signal=DEBUG_JTMS-SWDIO
PA14(JTCK/SWCLK).Signal=DEBUG_JTCK-SWCLK
PA15(JTDI).Signal=SPI3_NSS
PA1_C.GPIO_Label=ANALOG_IN_2
PA1_C.Signal=ADCx_INP1
PA2.Signal=ETH_MDIO
PA3.Signal=S_TIM5_CH4
PA4.Signal=COMP_DAC11_group
PA5.Signal=SPI1_SCK
PA6.Signal=S_TIM3_CH1
PA7.Signal=ETH_CRS_DV
PA8.Signal=RCC_MCO_1
PA9.Signal=USART1_TX
PB0.Signal=S_TIM3_CH3
PB1.Signal=S_TIM3_CH4
PB10.Signal=S_TIM2_CH3
PB11.Signal=S_TIM2_CH4
PB12.Signal=SPI2_NSS
PB13.Signal=ETH_TXD1
PB14.Signal=SPI2_MISO
PB15.Signal=SPI2_MOSI
PB2.Signal=SPI3_MOSI
PB3(JTDO/TRACESWO).Signal=S_TIM2_CH2
PB4(NJTRST).Signal=SPI1_MISO
PB5.Signal=S_TIM3_CH2
PB6.Signal=S_TIM4_CH1
PB7.Signal=S_TIM4_CH2
PB8.GPIO_Label=PWM_OUT_1
PB8.Signal=S_TIM16_CH1
PB9.GPIO_Label=PWM_OUT_2
PB9.Signal=S_TIM17_CH1
PC0.GPIO_Label=ANALOG_IN_5
PC0.Signal=ADCx_INP10
PC1.Signal=ETH_MDC
PC10.Signal=SPI3_SCK
PC11.Signal=SPI3_MISO
PC12.Signal=UART5_TX
PC13.GPIO_Label=EXTI13_WIFI
PC13.Signal=GPXTI13
PC14-OSC32_IN.GPIO_Label=EXTI14_FPGA_INT
PC14-OSC32_IN.Signal=GPXTI14
PC15-OSC32_OUT.GPIO_Label=EXTI15_FPGA_CDONE
PC15-OSC32_OUT.Signal=GPXTI15
PC2.Signal=OCTOSPIM_P1_IO2
PC2_C.GPIO_Label=ANALOG_IN_3
PC2_C.Signal=ADC3_INP0
PC3.Signal=OCTOSPIM_P1_IO6
PC3_C.GPIO_Label=ANALOG_IN_4
PC3_C.Signal=ADC3_INP1
PC4.Signal=ETH_RXD0
PC5.Signal=ETH_RXD1
PC6.Signal=S_TIM8_CH1
PC7.Signal=S_TIM8_CH2
PC8.Signal=S_TIM8_CH3
PC9.Signal=S_TIM8_CH4
PD0.Signal=UART4_RX
PD1.Signal=UART4_TX
PD10.GPIO_Label=SPI1_NSS_SW_1
PD10.Signal=GPIO_Output
PD11.Signal=OCTOSPIM_P1_IO0
PD12.Signal=OCTOSPIM_P1_IO1
PD13.Signal=OCTOSPIM_P1_IO3
PD14.Signal=S_TIM4_CH3
PD15.Signal=S_TIM4_CH4
PD2.Signal=UART5_RX
PD3.Signal=SPI2_SCK
PD4.Signal=OCTOSPIM_P1_IO4
PD5.Signal=USART2_TX
PD6.Signal=USART2_RX
PD7.Signal=SPI1_MOSI
PD8.Signal=USART3_TX
PD9.Signal=USART3_RX
PE0.Signal=UART8_RX
PE1.Signal=UART8_TX
PE10.Signal=OCTOSPIM_P1_IO7
PE11.Signal=S_TIM1_CH2
PE12.Signal=SPI4_SCK
PE13.Signal=S_TIM1_CH3
PE14.Signal=S_TIM1_CH4
PE15.GPIO_Label=OCTOSPI2_NCS_3
PE15.Signal=GPIO_Output
PE2.Signal=USART10_RX
PE3.Signal=USART10_TX
PE4.Signal=SPI4_NSS
PE5.Signal=SPI4_MISO
PE6.Signal=SPI4_MOSI
PE7.Signal=UART7_RX
PE8.Signal=UART7_TX
PE9.Signal=S_TIM1_CH1
PF0.Signal=TIM23_CH1
PF1.Signal=S_TIM23_CH2
PF10.Signal=OCTOSPIM_P1_CLK
PF11.Signal=TIM24_CH1
PF12.Signal=S_TIM24_CH2
PF13.Signal=S_TIM24_CH3
PF14.Signal=S_TIM24_CH4
PF15.GPIO_Label=FPGA_CRESET_B
PF15.Signal=GPIO_Output
PF2.Signal=S_TIM23_CH3
PF3.Signal=S_TIM23_CH4
PF4.Signal=OCTOSPIM_P2_CLK
PF5.GPIO_Label=SPI1_NSS_SW_2
PF5.Signal=GPIO_Input
PF6.Signal=SPI5_NSS
PF7.Signal=FDCAN3_TX
PF8.Signal=SPI5_MISO
PF9.Signal=SPI5_MOSI
PG0.Signal=UART9_RX
PG1.Signal=UART9_TX
PG10.Signal=FDCAN3_RX
PG11.Signal=ETH_TX_EN
PG12.Signal=OCTOSPIM_P2_NCS
PG13.Signal=ETH_TXD0
PG14.Signal=USART6_TX
PG15.GPIO_Label=SPI5_NSS_2
PG15.Signal=GPIO_Output
PG2.GPIO_Label=SPI3_NSS_2
PG2.Signal=GPIO_Output
PG3.GPIO_Label=SPI2_NSS_2
PG3.Signal=GPIO_Output
PG4.GPIO_Label=EXTI4_EMERGENCY_STOP
PG4.Signal=GPXTI4
PG5.Signal=S_TIM1_ETR
PG6.Signal=OCTOSPIM_P1_NCS
PG7.GPIO_Label=SPI4_NSS_2
PG7.Signal=GPIO_Output
PG8.Signal=S_TIM8_ETR
PG9.Signal=USART6_RX
PH0-OSC_IN.Signal=RCC_OSC_IN
PH1-OSC_OUT.GPIO_Label=OCTOSPI2_NCS_4
PH1-OSC_OUT.Signal=GPIO_Output
PH10.Signal=S_TIM5_CH1
PH11.Signal=S_TIM5_CH2
PH12.Signal=S_TIM5_CH3
PH13.Signal=FDCAN1_TX
PH14.Signal=FDCAN1_RX
PH15.GPIO_Label=OCTOSPI2_NCS_2
PH15.Signal=GPIO_Output
PH2.GPIO_Label=ANALOG_IN_6
PH2.Signal=ADC3_INP13
PH3.Signal=OCTOSPIM_P1_IO5
PH4.Signal=I2C2_SCL
PH5.Signal=I2C2_SDA
PH6.Signal=SPI5_SCK
PH7.Signal=I2C3_SCL
PH8.Signal=I2C3_SDA
PH9.GPIO_Label=EXTI9_DAC
PH9.Signal=GPXTI9

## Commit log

2026-01-27 Initial commit
    * Results from livestream on 2026/01/27
    [Requirements.ods, port peripheral mapping.xlsx]
2026-01-29 Add UFBGA176+25 variant. Update other design files.
    [Requirements.ods, port peripheral mapping.xlsx]
2026-01-29 Update UFBGA176+25 design. Major changes.
    [Requirements.ods, port peripheral mapping.xlsx]
2026-01-30 More design updates.
    [Requirements.ods, port peripheral mapping.xlsx]
2026-01-30 Initial schematic, based on the reversed engineers CHMT control board, but with the H7 and FPGA.
2026-01-31 Pin layout changes
    Removed:
    4, SPI2_NSS_2, SPI3_NSS_2, SPI4_NSS_2, SPI5_NSS_2
    3, SPI6_FPGA_CS, SPI6_WIFI_CS, SPI6_FLASH_CS
    6, PWM_OUT_A1-6
    4, DIGITAL_IN_1-4
    1, GPIO 15 wasn't used(!)
    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
    [port peripheral mapping.xlsx]
2026-02-01 Lots of schematic updates. Started on layout a little too.
    [port peripheral mapping.xlsx]
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2026-02-02 Many updates to schematic and layout.
    * Ethernet + USB
    * Dual channel MOSFETs
    * Connectors
    * Wifi location
    * More placement
2026-02-02 Update port/pin mappings.
    [Requirements.ods, port peripheral mapping.xlsx]
2026-02-02 Major update to the pin mapping.
    * no need for RTC / LSI.
    * no need for USB_ID.
    * dropped support for 2nd dac channel.
    * no need to pin-swap between uart4 and fdcan1 - simplifies software and hardware.
    * use spi1 instead of spi6
    * all uarts enabled
    * 2 PWM outputs on TIM16_CH1/TIM17_CH1.
    * i2c peripherals changed.
    * other pins moved.
    [port peripheral mapping.xlsx]
2026-02-02 Further changes to support conditional memory mapping of the FLASH, the WIFI, the FPGA (again) or a device on the expansion port.
    [port peripheral mapping.xlsx]
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2026-02-03 Analog MUX + more.
    [port peripheral mapping.xlsx]
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2026-02-06 FPGA, FLASH and INT updates.
    [port peripheral mapping.xlsx]
2026-02-06 Unknown changes.
    [port peripheral mapping.xlsx]
2026-02-07 PSU sequencing. LEDs. TCXO.
    [port peripheral mapping.xlsx]
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2026-02-11 Rework the side connectors a little.
2026-02-11 Major updates to the connectors. Added buzzer and USB socket for H7.
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2026-02-16 Update port/peripheral mapping.
    [port peripheral mapping.xlsx]
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2026-02-18 Misc updates. Fix regulator soldermask.
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2026-02-20 Major update to card detection system. FPGA IO assignment and analog muxes.
    [hx717 vro resistors.xlsx]
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2026-02-23 Re-assign FPGA IO. Phase 1 - rough cut into quadrants. Swap FPGA and MCU.
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2026-02-24 Re-order left hand connector pins. FPGA pins lower. Baseboard will need signal swaps on all 4 expansion ports.
2026-02-24 Major connector pin assignment rework. Moved many FPGA signals to the bottom of the left/right connectors which meant re-routing the base-board connectors too.
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2026-02-25 Swap TIM23/24 between left/right connectors. Route TIM23.
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2026-02-25 Update docs.
    [Requirements.ods, port peripheral mapping.xlsx]
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2026-02-27 Revert pcb layout due to some traces becoming unrouted.
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2026-02-27 Re-do route of LC_S1. Route PM1-4. Route I2C_MUX signals. Route buzzer
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2026-02-27 Rework bottom left connect. Route LA to it. Rework expansion connector.
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2026-03-03 Update note regarding USB cable clearance.
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2026-03-04 Update RS422 pinout. Adjust RS422 layout. Use V5B for AIN_EXT and RS422. More power and thermal optimizations. Fix AIN VAC silk pinouts. Add RS422 pinouts to silk.
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2026-03-04 Improve readability of Buzzer components in schematic.
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2026-03-04 Add USER0/1 buttons to CN_FL connector. Relocate buzzer signal.
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2026-03-04 Use RJ45/USB Combo jacks with integrated magnetics to reduce BOM and simplify things. Improve spacing around buzzer and button connectors.
2026-03-04 Updated port peripheral mappings.
    [port peripheral mapping.xlsx]
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2026-03-05 Fix transposed DI/DO between the ESP32-C6 and the flash.
2026-03-05 Replace the unique Samtech 20 pin connectors with more common variants using a custom high-density footprint and change the connectors to 22 pin variants. Add WIFI RX/TX to the right hand connector. 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
2026-03-06 Move WIFI_INT2 to IO8. Fix using OCTOSPI2_NCS_2 for flash CS instead of OCTOSPIM_P2_NCS. Added OCTOSPI2_NCS2 to IO14 where the WIFI_INT2 was. Added *_NCS net suffixes to prevent further confusion.
    * IO8 was unused anyway, except for boot control.
    * H7, FPGA and C6 now can all read/write the flash.
    * H7 can now correctly use OCTOSPI for the C6.
    [port peripheral mapping.xlsx]
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2026-03-06 Fix a trace that got deleted instead of the stub via it was connected to.
2026-03-06 Fix 5V PGOOD input signals. Use a power supervisor to generate a board-local PGOOD input instead of relying on an external trigger.
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2026-03-09 Fix thermals on P1-4 connectors.
    * Error with copper pours.
2026-03-09 Fix voltage rating of 100nF caps around PM1-4
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2026-03-10 Fix pin name on U6
2026-03-10 Cleanups and release to manufacturing.
    [1 - Top.gbr, 2 - GND.gbr, 2 - Power_Signal 1.gbr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]
2026-03-10 Initial PnP files.
    [MakerPnPControl-PnP.csv, MakerPnPControl-core-PnP.csv]
2026-03-11 Update exported files. Schematic component cleanups. Change LED resistors to 0402. Add variant builder files (part mappings, parts, substitutions, args). Add variant builder output files.
    [1 - Top.gbr, 2 - Power_Signal 1.gbr, 3 - GND.gbr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]
2026-03-12 Schematic, placement and BOM updates.
    [MakerPnPControl-core-BOM.csv, MakerPnPControl-core-PnP.csv, MakerPnPControl-core-PnP_variant1.csv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]
2026-03-12 Update core CPL file.
    [MakerPnPControl-core_variant1_cpl.csv, MakerPnPControl-core_variant1_cpl.xlsx]
2026-03-12 base board schematic updates. BOM, PnP files, etc.
    [MakerPnPControl-BOM.csv, MakerPnPControl-PnP.csv, MakerPnPControl_variant1_bom.csv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]
2026-03-12 base board updates in prep for PCBA.
    [MakerPnPControl-BOM.csv, MakerPnPControl-PnP.csv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]
2026-03-13 Add cpl files for JLCPCB.
    [MakerPnPControl_variant1_cpl.csv, MakerPnPControl_variant1_cpl.xlsx]
2026-03-13 Updates based on changes made during the ordering process.
    [MakerPnPControl_variant1_bom.csv, MakerPnPControl_variant1_placements.csv, MakerPnPControl_variant1_substitutions.csv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]
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2026-03-20 Remove old layer export files.
    [2 - Power_Signal.gbr, 3 - GND.gbr]
2026-03-20 Autosaved file.
    [MakerPnPControl-core_variant1_cpl.xlsx]
2026-03-20 Update the directory layout. Update the readme. Update the args files.
    [1 - Top.gbr, 2 - GND.gbr, 2 - Power_Signal 1.gbr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]
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2026-03-24 Use parallel current sense resistors. Attempt phase routing.
    * need to swap motor output pins on connector.
2026-03-24 fixed motor phases
2026-03-24 Rework motor connector position to allow for a heatskink again. Add heatsink mounting holes.
    * heatsink was forgot about that when the fets were changed...
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2026-03-25 Fix schematic DRC errors.
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2026-03-26 Add variant builder files for the stepper expansion.
    [MakerPnPControl-stepper1-BOM.csv, MakerPnPControl-stepper1-PnP.csv, MakerPnPControl-stepper1_variant1_rules.csv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]
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2026-03-26 Prep some variant1 manufacturing files. Create BOM and PnP files. Various schematic updates. Silk screen updates.
    [MakerPnPControl-stepper1-BOM.csv, MakerPnPControl-stepper1-PnP.csv, MakerPnPControl-stepper1_variant1_bom.csv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]
2026-03-26 Tweaks to paste, mask, silk. Export more PDF files.
    [1 - Top.gbr, 2 - GND.gbr, 3 - Power_Signal.gbr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]
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2026-03-27 Via and pad cleanups. Board outline needs to be 50mm wide minimum for bevelled edge.
    [1 - Top.gbr, 2 - GND.gbr, 3 - Power_Signal.gbr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]
2026-03-27 Re-run variant builder.
    [MakerPnPControl-stepper1-PnP.csv, MakerPnPControl-stepper1_variant1_placements.csv]
2026-03-27 Changes due to manufacturing/assembly review.
    [MakerPnPControl-stepper1-BOM.csv, MakerPnPControl-stepper1-PnP.csv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]
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2026-03-29 Update MOVs, cleanup, export.
    [1 - Top.gbr, 2 - GND.gbr, 3 - Power_Signal.gbr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]
2026-03-29 Updates to BOM and placements.
    [MakerPnPControl-stepper1_variant1_bom.csv, MakerPnPControl-stepper1_variant1_placements.csv, global-substitutions.csv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]
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2026-04-04 Update silk on Power connector. Add TVS diode on 5V. Fix 3v3 reg EN inputs by pulling V1P2 PGOOD to 5V.
    [1 - Top.gbr, 2 - Power_Signal 1.gbr, 3 - GND.gbr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]
2026-05-07 Fix incorrect part mapping for 60R4 resistors. They were previously mapped to 49R9.
    [part-mappings.csv, parts.csv]
2026-05-07 Fix incorrect part listing and part mapping for 22uF 25V 0805 caps.
    * They were mapped to 100nF 0402s, this made it all the way though the prototype production without being spotted.
    #REWORK
    [part-mappings.csv, parts.csv]
2026-05-07 Update the BOM, Placements and CPL files with the correct components.
    * refer to the diff to see affected refdes/components.
    [MakerPnPControl-base_variant1_bom.csv, MakerPnPControl-base_variant1_placements.csv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]
2026-05-07 Fix mishap with a route keepout. Fix missing solder mask keepout on layer window. Fix layer window layers 2 and 3.
    * layers 2 and 3 were swapped, but the window wasn't updated.
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2026-05-07 Base - Fix inverted polarity of D2 status led.
    * this was caught before rev A1 went into production and changed during assembly.
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2026-05-08 Base - Replace ADuM1200 with ADMuM120N0 due to power sequencing/failsafe issues on PM1-4 outputs.
2026-05-08 Remove duplicate MFR+MPN.
    [parts.csv]
2026-05-22 Core - Update revision history / errata and workarounds/hack details. Update schematic a little.
2026-05-27 The USB+RJ45 connector, HR981190C, isn't pin compatible with the RJMG1331171C1ER, use DGUK611U2B101DB2WD instead.
    [MakerPnPControl-base_variant1_bom.csv, MakerPnPControl-base_variant1_placements.csv, global-substitutions.csv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]
2026-05-27 Missing VDDIO voltage on the ETH PHY.
    * errata updated.
    * schematic corrected.
    * PCB needs re-routing still.
2026-05-27 Fix incorrect part listing and part mapping for 22uF 25V 0805 caps on the stepper board.
    See 09274a0171d598c4677665caaae5030f4486db21
    [MakerPnPControl-stepper1_variant1_bom.csv, MakerPnPControl-stepper1_variant1_placements.csv]
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2026-06-01 Add errata for stepper1 board. Power sequencing issue. Transposed FET input/feedback signals.
2026-06-23 Stepper1 - Add missing silk screen todo item.
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
